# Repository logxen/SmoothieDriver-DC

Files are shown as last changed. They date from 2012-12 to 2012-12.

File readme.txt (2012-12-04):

OVERVIEW

SmoothieDriver is a series of motor controllers designed to interface with Smoothieboard and other RepRap style motion controllers, allowing an enable/direction/step interface like the Pololu A4988 breakout boards commonly used and optionally i2c block level control with closed-loop feedback for advanced systems.

SmoothieDriver-DC is a series of Full H-Bridge drivers with closed-loop encoder feedback for driving Brush DC Motors. The system allows Brushed DC Motors to be controlled much like a stepper motor.

The current prototype board (gamma) is a triple motor driver capable of up to 3.5A per motor.

For more information contact Logxen. He is easily found on irc.freenode.net in #smoothieware or by e-mail at reprap at logxen dot com.

MAJOR COMPONENTS

SmoothieDriver-DC Gamma uses an NXP LPC1114, which has an Arm Cortex-M0 core, as mcu. It drives up to three Allegro a4950 full h-bridge drivers with current control managed by an MCP4725 on each driver. An upgrade from the Beta version, Gamma includes an MCP1252 3.3V regulator on-board so that it can be safely driven from a 3.3V or a 5V motion controller.

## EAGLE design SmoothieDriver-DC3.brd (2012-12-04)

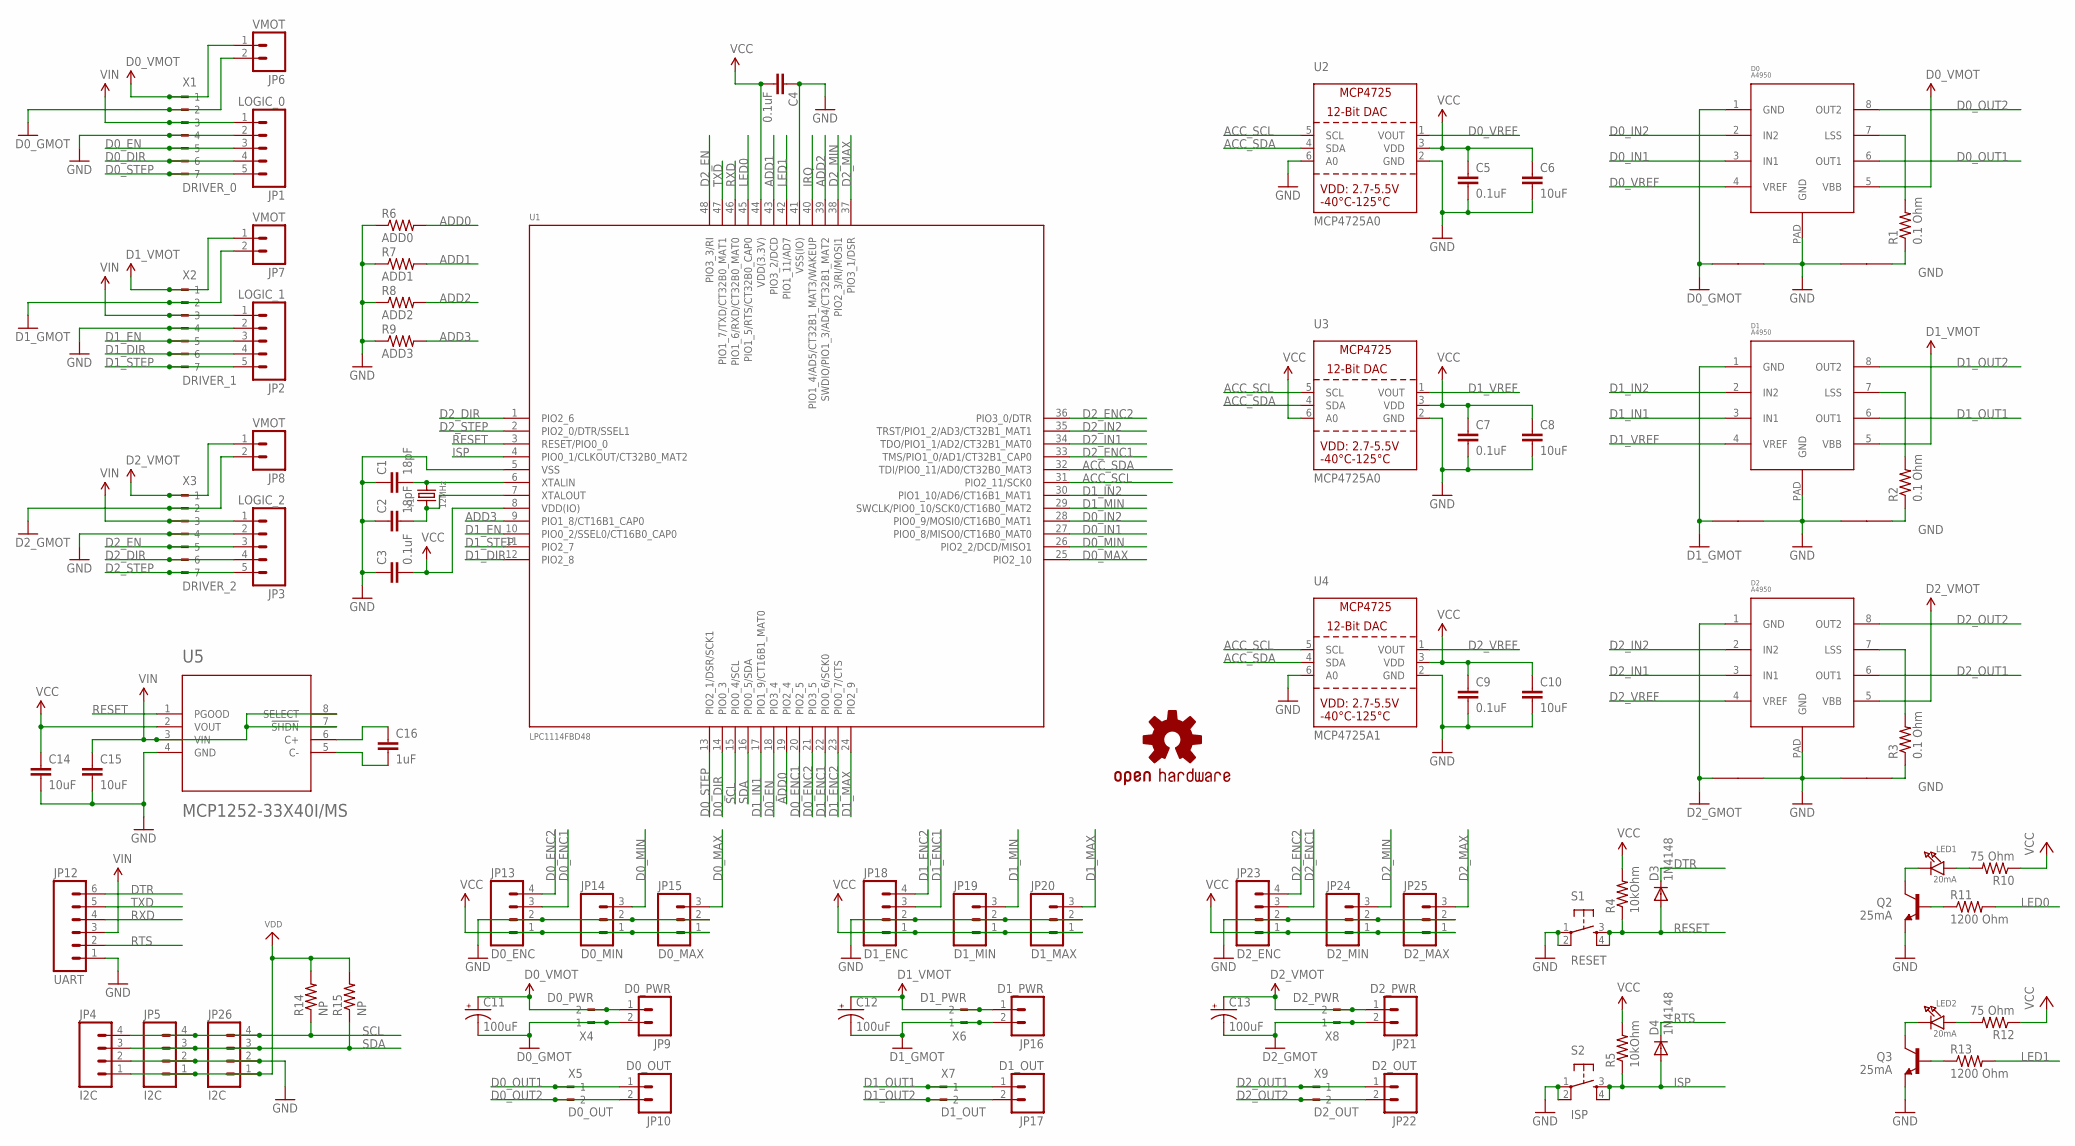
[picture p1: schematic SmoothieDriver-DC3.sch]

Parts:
C1, C2: 18pF; 0603-CAP
C3, C4, C5, C7, C9: 0.1uF; 0603-CAP
C6, C8, C10: 10uF; 0603-CAP
C11, C12, C13: 100uF; PANASONIC_E
C14, C15: 10uF; 1206
C16: 1uF; 0805
D0, D1, D2: A4950; SOICN8-PAD
D0_GMOT: NET_LINK
D3, D4: 1N4148; SOD523
JP1: LOGIC_0; 1X05
JP2: LOGIC_1; 1X05
JP3: LOGIC_2; 1X05
JP4, JP5, JP26: I2C; 1X04
JP6, JP7, JP8: VMOT; 1X02
JP9: D0_PWR; 1X02
JP10: D0_OUT; 1X02
JP12: UART; 1X06
JP13: D0_ENC; 1X04
JP14: D0_MIN; 1X03
JP15: D0_MAX; 1X03
JP16: D1_PWR; 1X02
JP17: D1_OUT; 1X02
JP18: D1_ENC; 1X04
JP19: D1_MIN; 1X03
JP20: D1_MAX; 1X03
JP21: D2_PWR; 1X02
JP22: D2_OUT; 1X02
JP23: D2_ENC; 1X04
JP24: D2_MIN; 1X03
JP25: D2_MAX; 1X03
LED1, LED2: 20mA; CHIPLED_0805
Q2, Q3: 25mA; SOT23
R1, R2, R3: 0.1 Ohm; R2512
R4, R5: 10kOhm; 0603-RES
R6: ADD0; 0603-RES
R7: ADD1; 0603-RES
R8: ADD2; 0603-RES
R9: ADD3; 0603-RES
R10, R12: 75 Ohm; R0603
R11, R13: 1200 Ohm; R0603
R14, R15: NP; 0603-RES
S1: RESET; TACTILE_SWITCH_SMD
S2: ISP; TACTILE_SWITCH_SMD
U1: LPC1114FBD48; LQFP48
U2, U3: MCP4725A0; SOT23-6
U4: MCP4725A1; SOT23-6
U5: MCP1252-33X40I/MS; MSOP8_0.65MM
U$15: OSHW-LOGOM; OSHW-LOGO-M
U$22, U$23, U$24, U$25, U$26: NET_LINK
X1: DRIVER_0; 180-7
X2: DRIVER_1; 180-7
X3: DRIVER_2; 180-7
X4: D0_PWR; 180-2
X5: D0_OUT; 180-2
X6: D1_PWR; 180-2
X7: D1_OUT; 180-2
X8: D2_PWR; 180-2
X9: D2_OUT; 180-2
Y1: 12MHz; CRYSTAL_3.2X2.5

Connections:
ACC_SCL: U1.31 (PIO2_11/SCK0), U2.5 (SCL), U3.5 (SCL), U4.5 (SCL)
ACC_SDA: U1.32 (TDI/PIO0_11/AD0/CT32B0_MAT3), U2.4 (SDA), U3.4 (SDA), U4.4 (SDA)
ADD0: R6.2, U1.19 (PIO2_4)
ADD1: R7.2, U1.43 (PIO3_2/DCD)
ADD2: R8.2, U1.39 (SWDIO/PIO1_3/AD4/CT32B1_MAT2)
ADD3: R9.2, U1.9 (PIO1_8/CT16B1_CAP0)
D0_DIR: JP1.4, U1.14 (PIO0_3), X1.6
D0_EN: JP1.3, U1.18 (PIO3_4), X1.5
D0_ENC1: JP13.3, U1.20 (PIO2_5)
D0_ENC2: JP13.4, U1.21 (PIO3_5)
D0_GMOT: C11.-, D0.1 (GND), D0_GMOT.P$1, JP6.2, JP9.2, X1.2, X4.1
D0_IN1: D0.3 (IN1), U1.27 (PIO0_8/MISO0/CT16B0_MAT0)
D0_IN2: D0.2 (IN2), U1.28 (PIO0_9/MOSI0/CT16B0_MAT1)
D0_LSS: D0.7 (LSS), R1.2
D0_MAX: JP15.3, U1.25 (PIO2_10)
D0_MIN: JP14.3, U1.26 (PIO2_2/DCD/MISO1)
D0_OUT1: D0.6 (OUT1), JP10.1, X5.1
D0_OUT2: D0.8 (OUT2), JP10.2, X5.2
D0_STEP: JP1.5, U1.13 (PIO2_1/DSR/SCK1), X1.7
D0_VMOT: C11.+, D0.5 (VBB), JP6.1, JP9.1, X1.1, X4.2
D0_VREF: D0.4 (VREF), U2.1 (VOUT)
D1_DIR: JP2.4, U1.12 (PIO2_8), X2.6
D1_EN: JP2.3, U1.10 (PIO0_2/SSEL0/CT16B0_CAP0), X2.5
D1_ENC1: JP18.3, U1.22 (PIO0_6/SCK0)
D1_ENC2: JP18.4, U1.23 (PIO0_7/CTS)
D1_GMOT: C12.-, D1.1 (GND), JP7.2, JP16.2, U$23.P$1, X2.2, X6.1
D1_IN1: D1.3 (IN1), U1.17 (PIO1_9/CT16B1_MAT0)
D1_IN2: D1.2 (IN2), U1.30 (PIO1_10/AD6/CT16B1_MAT1)
D1_LSS: D1.7 (LSS), R2.2
D1_LSS1: D2.7 (LSS), R3.2
D1_MAX: JP20.3, U1.24 (PIO2_9)
D1_MIN: JP19.3, U1.29 (SWCLK/PIO0_10/SCK0/CT16B0_MAT2)
D1_OUT1: D1.6 (OUT1), JP17.1, X7.1
D1_OUT2: D1.8 (OUT2), JP17.2, X7.2
D1_STEP: JP2.5, U1.11 (PIO2_7), X2.7
D1_VMOT: C12.+, D1.5 (VBB), JP7.1, JP16.1, X2.1, X6.2
D1_VREF: D1.4 (VREF), U3.1 (VOUT)
D2_DIR: JP3.4, U1.1 (PIO2_6), X3.6
D2_EN: JP3.3, U1.48 (PIO3_3/RI), X3.5
D2_ENC1: JP23.3, U1.33 (TMS/PIO1_0/AD1/CT32B1_CAP0)
D2_ENC2: JP23.4, U1.36 (PIO3_0/DTR)
D2_GMOT: C13.-, D2.1 (GND), JP8.2, JP21.2, U$26.P$1, X3.2, X8.1
D2_IN1: D2.3 (IN1), U1.34 (TDO/PIO1_1/AD2/CT32B1_MAT0)
D2_IN2: D2.2 (IN2), U1.35 (TRST/PIO1_2/AD3/CT32B1_MAT1)
D2_MAX: JP25.3, U1.37 (PIO3_1/DSR)
D2_MIN: JP24.3, U1.38 (PIO2_3/RI/MOSI1)
D2_OUT1: D2.6 (OUT1), JP22.1, X9.1
D2_OUT2: D2.8 (OUT2), JP22.2, X9.2
D2_STEP: JP3.5, U1.2 (PIO2_0/DTR/SSEL1), X3.7
D2_VMOT: C13.+, D2.5 (VBB), JP8.1, JP21.1, X3.1, X8.2
D2_VREF: D2.4 (VREF), U4.1 (VOUT)
DTR: D3.C, JP12.6
GND: C1.1, C2.1, C3.1, C4.1, C5.2, C6.2, C7.2, C8.2, C9.2, C10.2, C14.2, C15.2, D0.PAD (GND), D0_GMOT.P$2, D1.PAD (GND), D2.PAD (GND), JP1.2, JP2.2, JP3.2, JP4.2, JP5.2, JP12.1, JP13.2, JP14.2, JP15.2, JP18.2, JP19.2, JP20.2, JP23.2, JP24.2, JP25.2, JP26.2, Q2.2 (E), Q3.2 (E), R1.1, R2.1, R3.1, R6.1, R7.1, R8.1, R9.1, S1.1, S1.2, S2.1, S2.2, U1.5 (VSS), U1.41 (VSS(IO)), U2.2 (GND), U2.6 (A0), U3.2 (GND), U4.2 (GND), U4.6 (A0), U5.4 (GND), U$22.P$1, U$22.P$2, U$23.P$2, U$24.P$1, U$24.P$2, U$25.P$1, U$25.P$2, U$26.P$2, X1.4, X2.4, X3.4
IRQ: U1.40 (PIO1_4/AD5/CT32B1_MAT3/WAKEUP)
ISP: D4.A, R5.1, S2.3, S2.4, U1.4 (PIO0_1/CLKOUT/CT32B0_MAT2)
LED0: R11.2, U1.45 (PIO1_5/RTS/CT32B0_CAP0)
LED1: R13.2, U1.42 (PIO1_11/AD7)
unnamed: LED1.A, R10.2
unnamed: LED1.C, Q2.3 (C)
unnamed: Q2.1 (B), R11.1
unnamed: Q3.1 (B), R13.1
unnamed: LED2.A, R12.2
unnamed: LED2.C, Q3.3 (C)
PWRREG_C+: C16.1, U5.6 (C+)
PWRREG_C-: C16.2, U5.5 (C-)
RESET: D3.A, R4.1, S1.3, S1.4, U1.3 (RESET/PIO0_0), U5.1 (PGOOD)
RTS: D4.C, JP12.2
RXD: JP12.4, U1.46 (PIO1_6/RXD/CT32B0_MAT0)
SCL: JP4.4, JP5.4, JP26.4, R14.1, U1.15 (PIO0_4/SCL)
SDA: JP4.3, JP5.3, JP26.3, R15.1, U1.16 (PIO0_5/SDA)
TXD: JP12.5, U1.47 (PIO1_7/TXD/CT32B0_MAT1)
VCC: C3.2, C4.2, C5.1, C6.1, C7.1, C8.1, C9.1, C10.1, C14.1, JP13.1, JP14.1, JP15.1, JP18.1, JP19.1, JP20.1, JP23.1, JP24.1, JP25.1, R4.2, R5.2, R10.1, R12.1, U1.8 (VDD(IO)), U1.44 (VDD(3.3V)), U2.3 (VDD), U3.3 (VDD), U3.6 (A0), U4.3 (VDD), U5.2 (VOUT)
VDD: JP4.1, JP5.1, JP26.1, R14.2, R15.2
VIN: C15.1, JP1.1, JP2.1, JP3.1, JP12.3, U5.3 (VIN), U5.7 (!SHDN), U5.8 (SELECT), X1.3, X2.3, X3.3
XTALIN: C1.2, U1.6 (XTALIN), Y1.2
XTALOUT: C2.2, U1.7 (XTALOUT), Y1.1

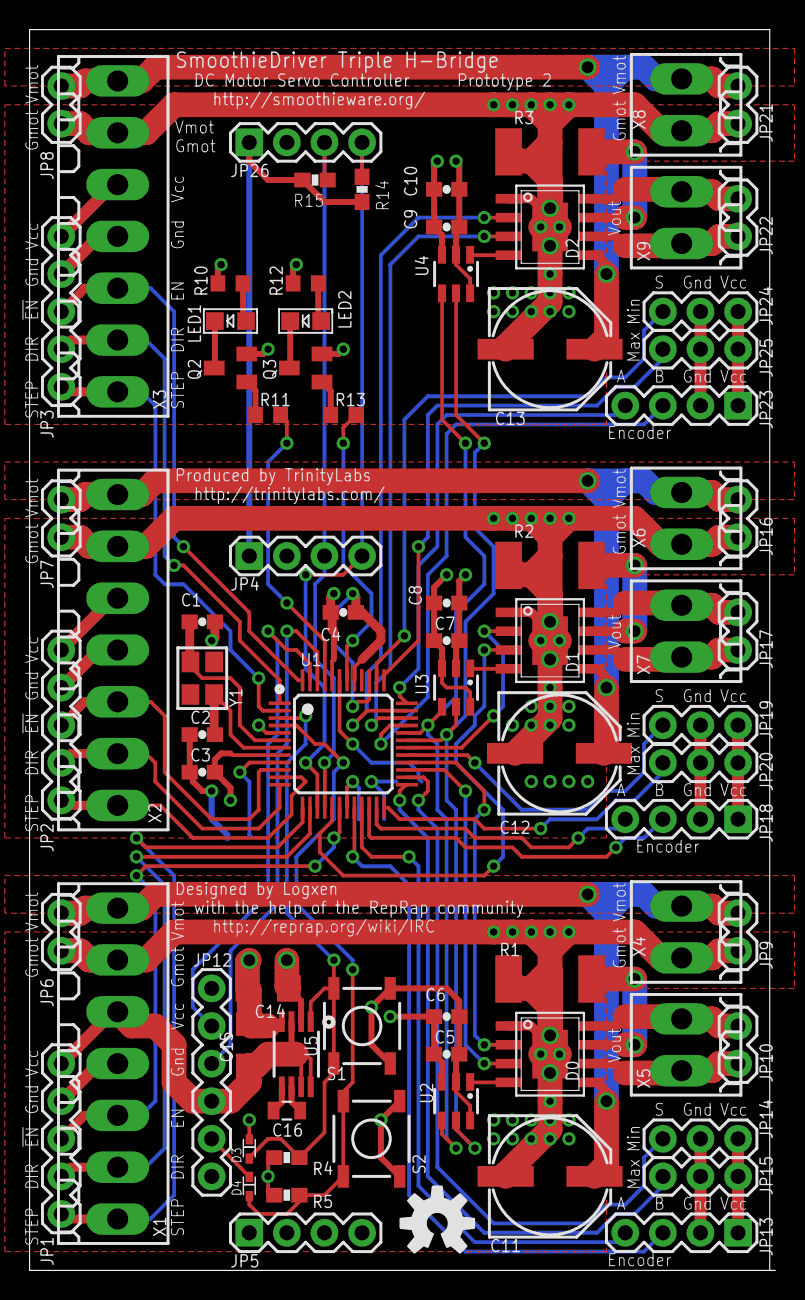
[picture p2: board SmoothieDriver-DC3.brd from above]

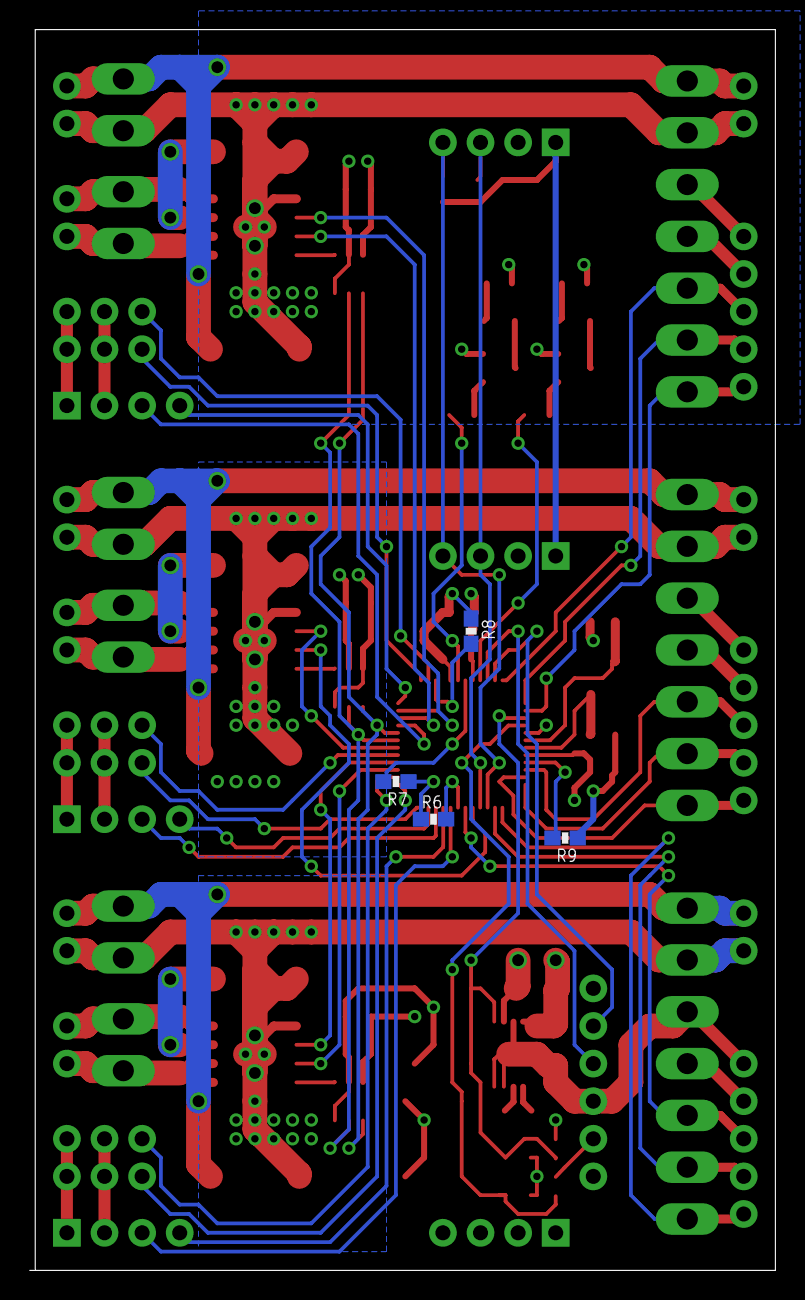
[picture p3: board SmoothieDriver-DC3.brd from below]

Board: 4 copper layers, 50.0 x 83.8 mm, 89 parts (5 on the bottom side), 75 nets.

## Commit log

2012-11-21 Innitial commit of DC-3 Gamma board
    [SmoothieDriver-DC3.brd, SmoothieDriver-DC3.sch]
2012-12-04 Prototype 2 as sent to board house
    [SmoothieDriver-DC3.brd, SmoothieDriver-DC3.sch]

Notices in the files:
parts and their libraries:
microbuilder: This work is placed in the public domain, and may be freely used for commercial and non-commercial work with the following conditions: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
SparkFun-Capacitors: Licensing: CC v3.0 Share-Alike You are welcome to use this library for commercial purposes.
